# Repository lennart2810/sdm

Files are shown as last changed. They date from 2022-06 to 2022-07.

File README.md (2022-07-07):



<div align="center">
  <a href="https://www.w-hs.de/maschinenbau-master-boh/">
    Images
  </a>
</div>
<h1 align="center"> Special Topics of Mechatronics <br> Inverted Pendulum </h1>

<br/>
<div align="center">
  <a href="https://github.com/lennart2810/sdm/blob/master/CAD/assembly_screenshot.png">
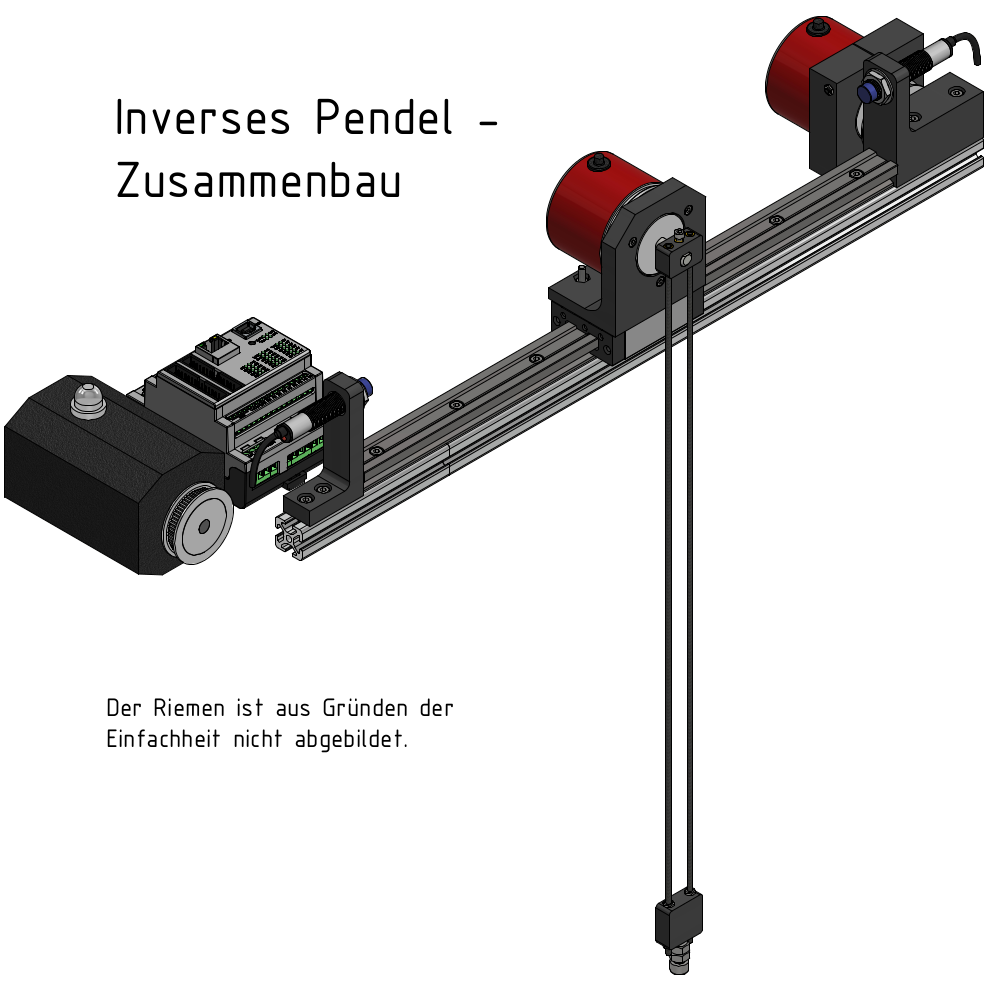
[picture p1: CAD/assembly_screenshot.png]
Images
    
  </a>
</div>
<br>

   ```sh
   git clone https://github.com/lennart2810/sdm.git
   ```

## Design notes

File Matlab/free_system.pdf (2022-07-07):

## Special Topics of Mechatronics - Inverted Pendulum

### Prepare Simscape Multibody Simulation

Import CAD files, created by Simscape Multibody Link, via Command Window:

smimport('invertedPendulum'); % .xml-file
Run invertedPendulum_DataFile.m, generated by the smimport-function, to load CAD parameter.

The data in this file sets the block parameter values in the Simscape Multibody model.

inverted_pendulum_DataFile;

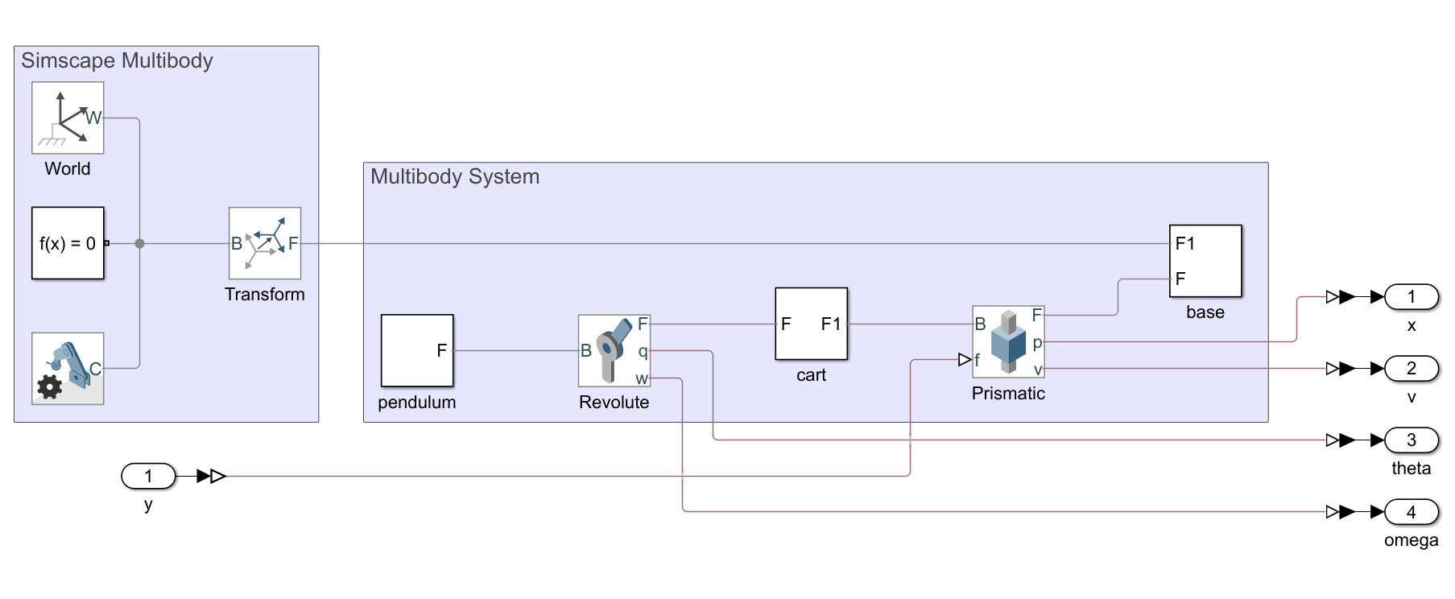
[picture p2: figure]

### Prepare Simscape Multibody Simulation

(overwrite some of the invertedPendulum_DataFile.m params)

% starting positions
x_0 = 0; | % [m] (0m --> middle of the track)
theta_0 = 4; | % [deg] (0° --> upright)

% starting velocities
v_0 = 0; | % [m/s]
omega_0 = 0; | % [deg/s]

% damping
D = 0.00001; | % [N/(m/s)] track-cart damping
d = 0.000001; | % [N*m/(deg/s)] cart-pendulum damping

### Run Simulation

filename = 'free_system.slx'; %open(filename);
sim_data = sim(filename);

### Show timeseries plots

plot(sim_data.find('x'));
hold on;
plot(sim_data.find('theta')); hold off;

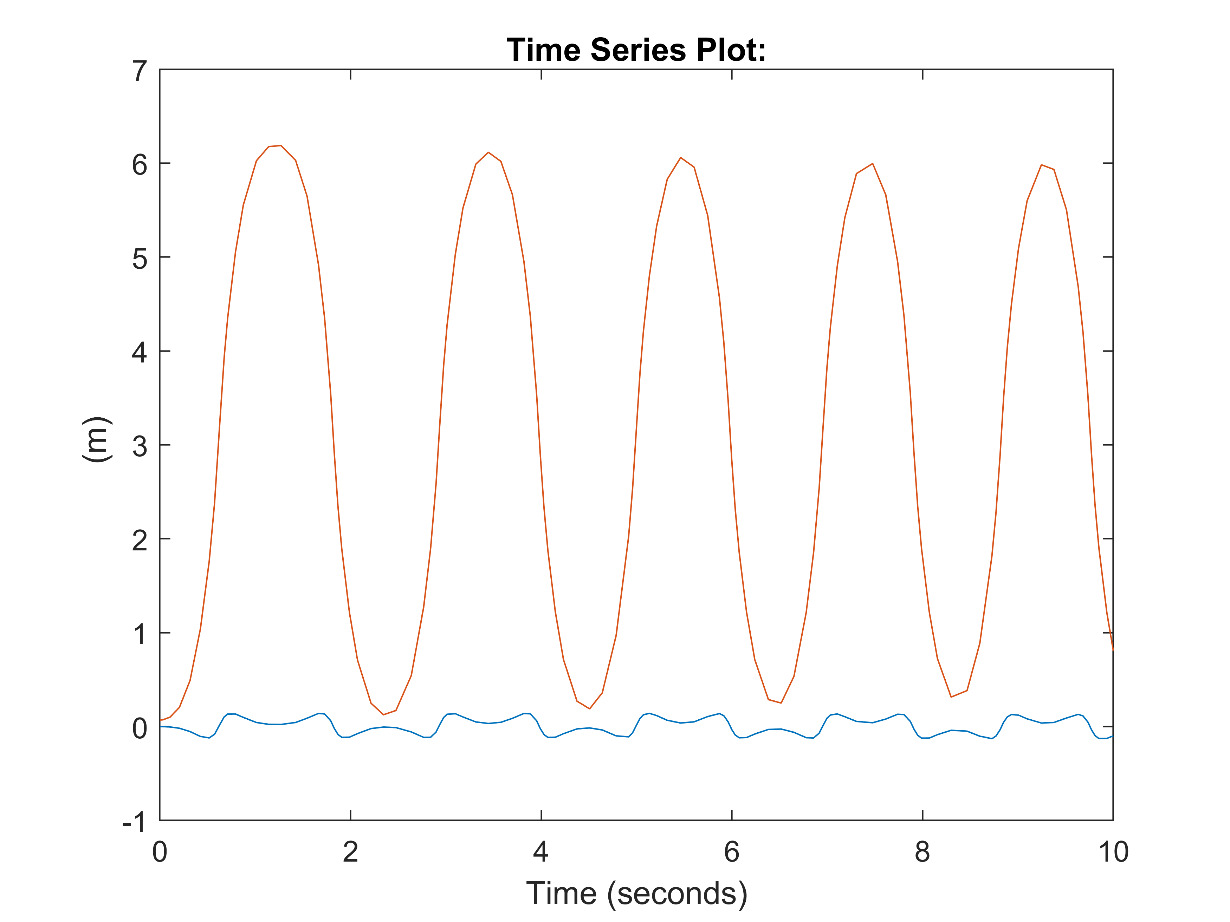
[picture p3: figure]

plot(sim_data.find('v'));
hold on;
plot(sim_data.find('omega'));

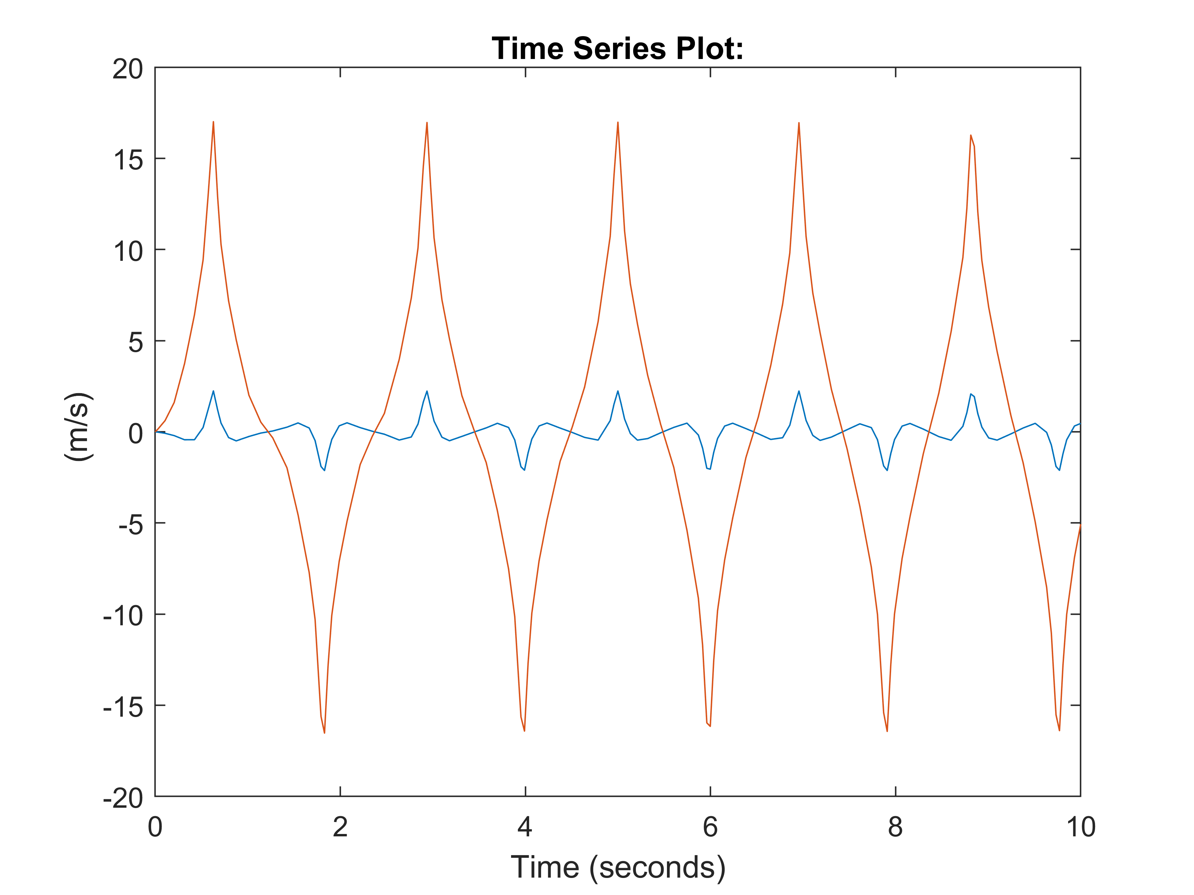
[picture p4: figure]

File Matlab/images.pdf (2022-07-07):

## Special Topics of Mechatronics - Inverted Pendulum - Images

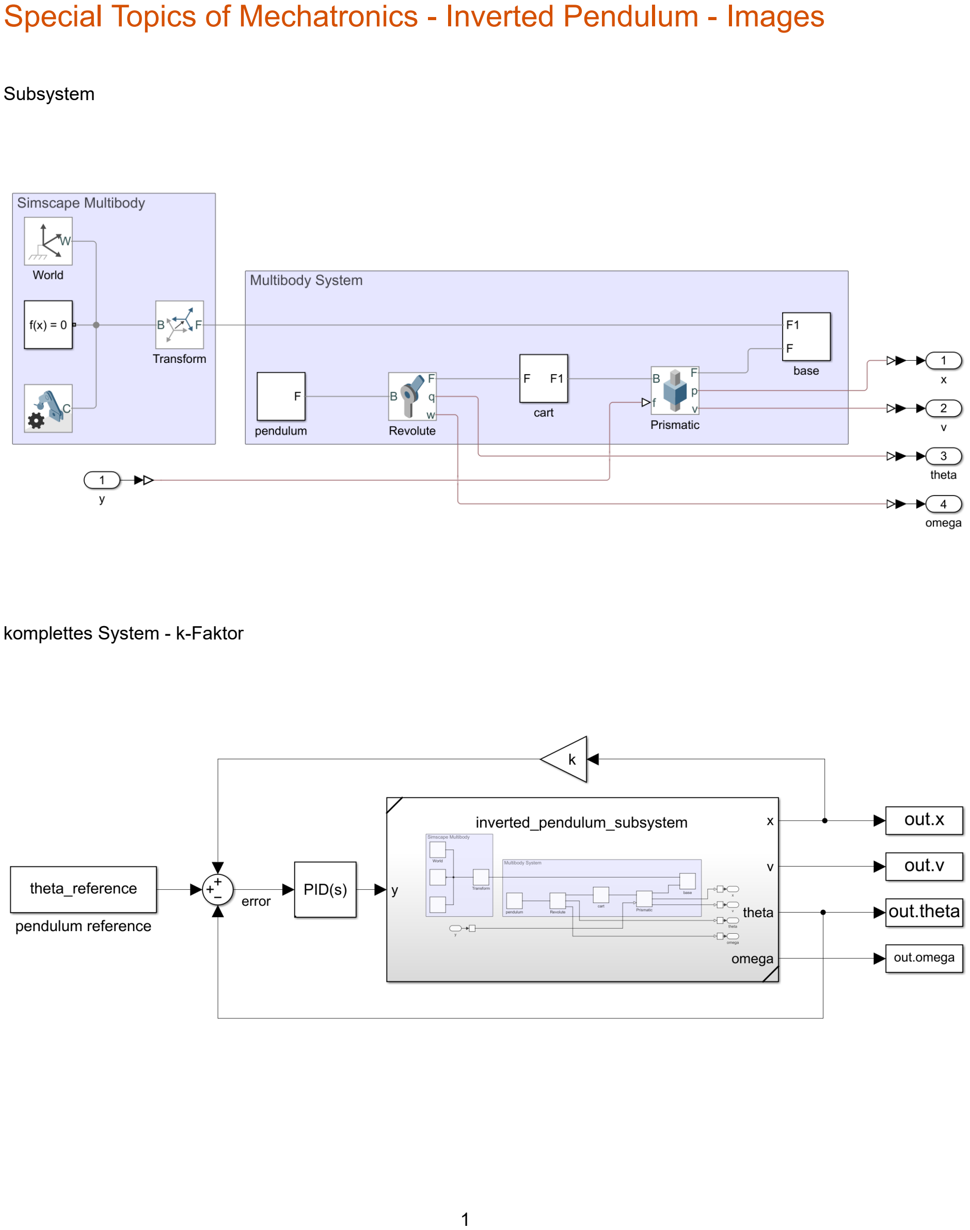
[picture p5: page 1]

Subsystem

komplettes System - k-Faktor

1

komplettes System - PID

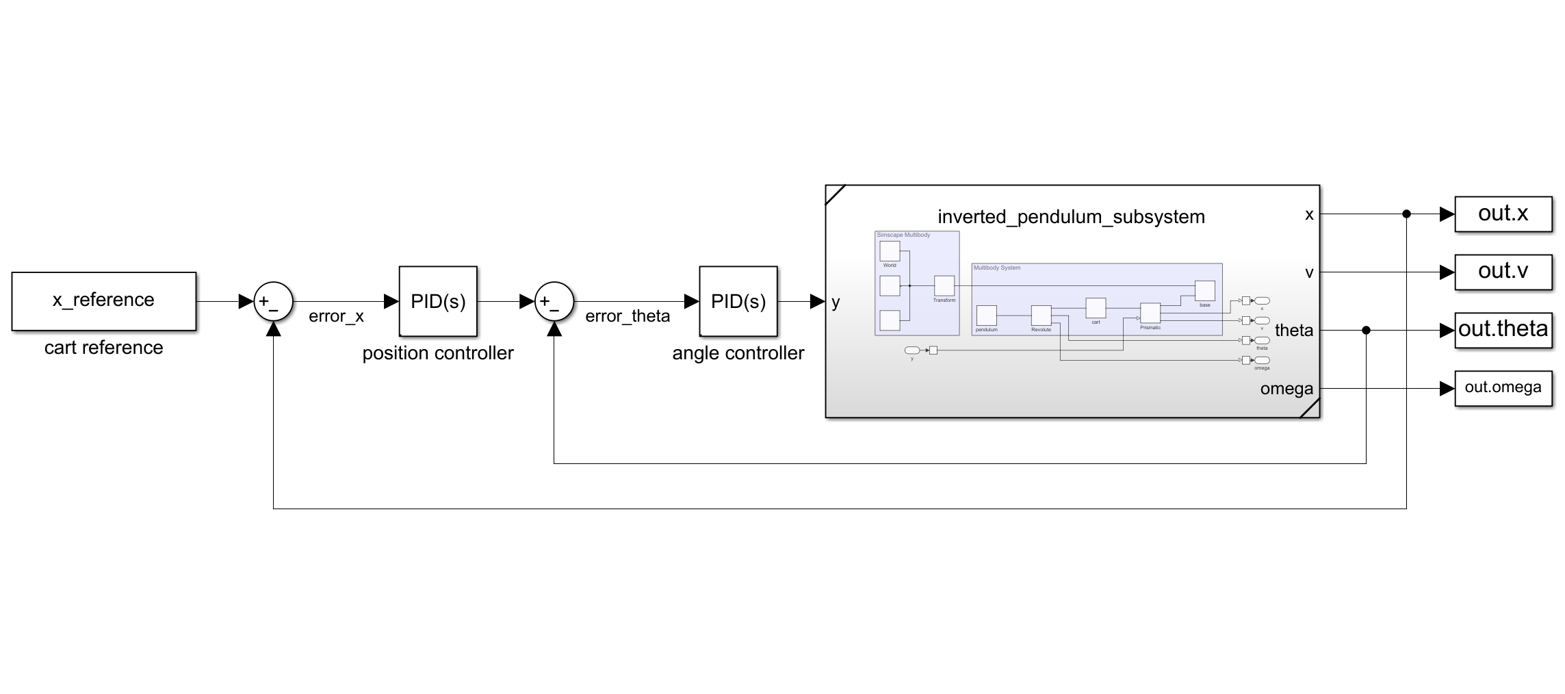
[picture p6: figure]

2

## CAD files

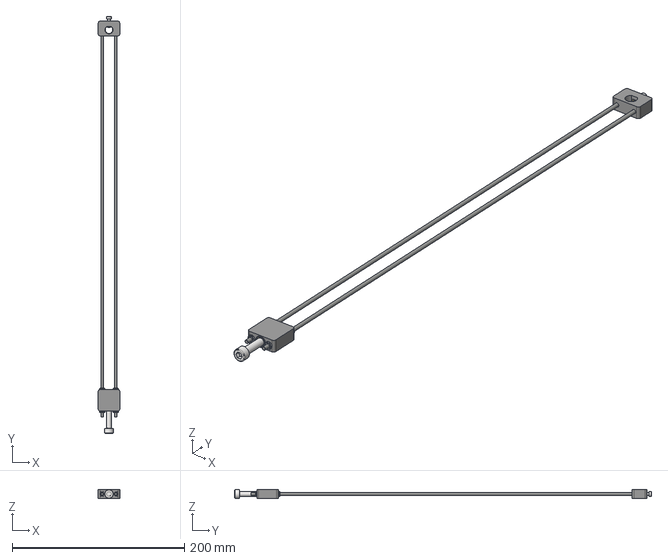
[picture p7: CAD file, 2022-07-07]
Matlab/pendulum_assembly_ipt_18ce7060.STEP
25.0 x 484.4 x 10.0 mm

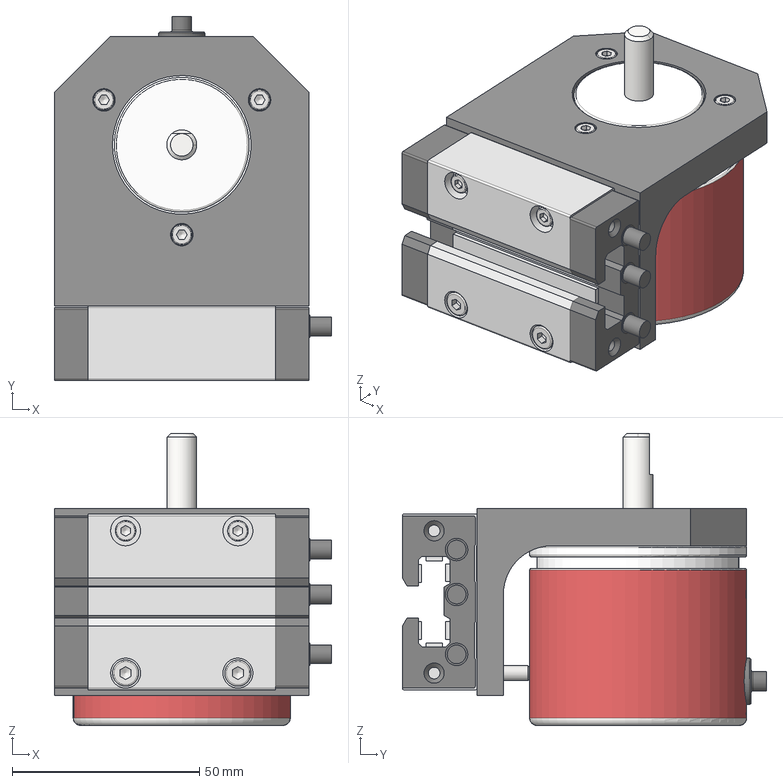
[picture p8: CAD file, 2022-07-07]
Matlab/cart_assembly_ipt_f98a6c2.STEP
74.0 x 97.3 x 78.0 mm

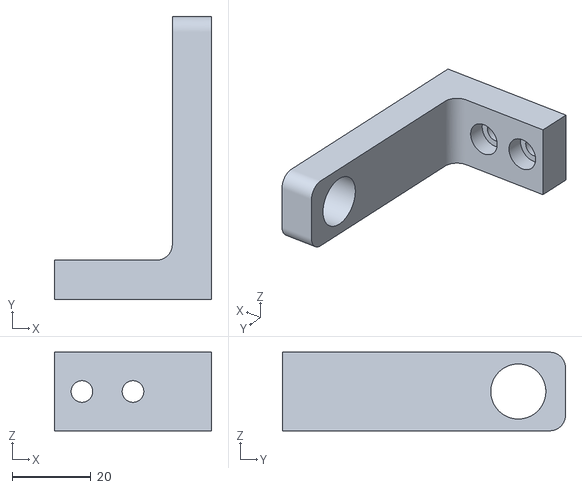
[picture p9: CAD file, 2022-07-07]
CAD/inductive_sensor_adapter.stl
40.0 x 72.0 x 20.0

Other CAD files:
CAD/M3_threaded_rod_460.ipt
CAD/M3_threaded_rod_70.ipt
CAD/M3_tread_insert.ipt
CAD/M4_groove_stone.ipt
CAD/assembly.iam
CAD/assembly_drawing.idw
CAD/base_assembly.iam
CAD/cart.ipt
CAD/cart_assembly.iam
CAD/cart_assembly.ipt
CAD/clamping_insert.ipt
CAD/dunkermotor.ipt
CAD/encoder_adapter.ipt
CAD/gt2_60.ipt
CAD/inductive_sensor.ipt
CAD/inductive_sensor_adapter.ipt
CAD/item_profile.ipt
CAD/opkon_encoder.ipt
CAD/pendulum_adapter.ipt
CAD/pendulum_assembly.iam
CAD/pendulum_assembly.ipt
CAD/pendulum_mass.ipt
CAD/pulley_positioner.ipt
CAD/rail.ipt

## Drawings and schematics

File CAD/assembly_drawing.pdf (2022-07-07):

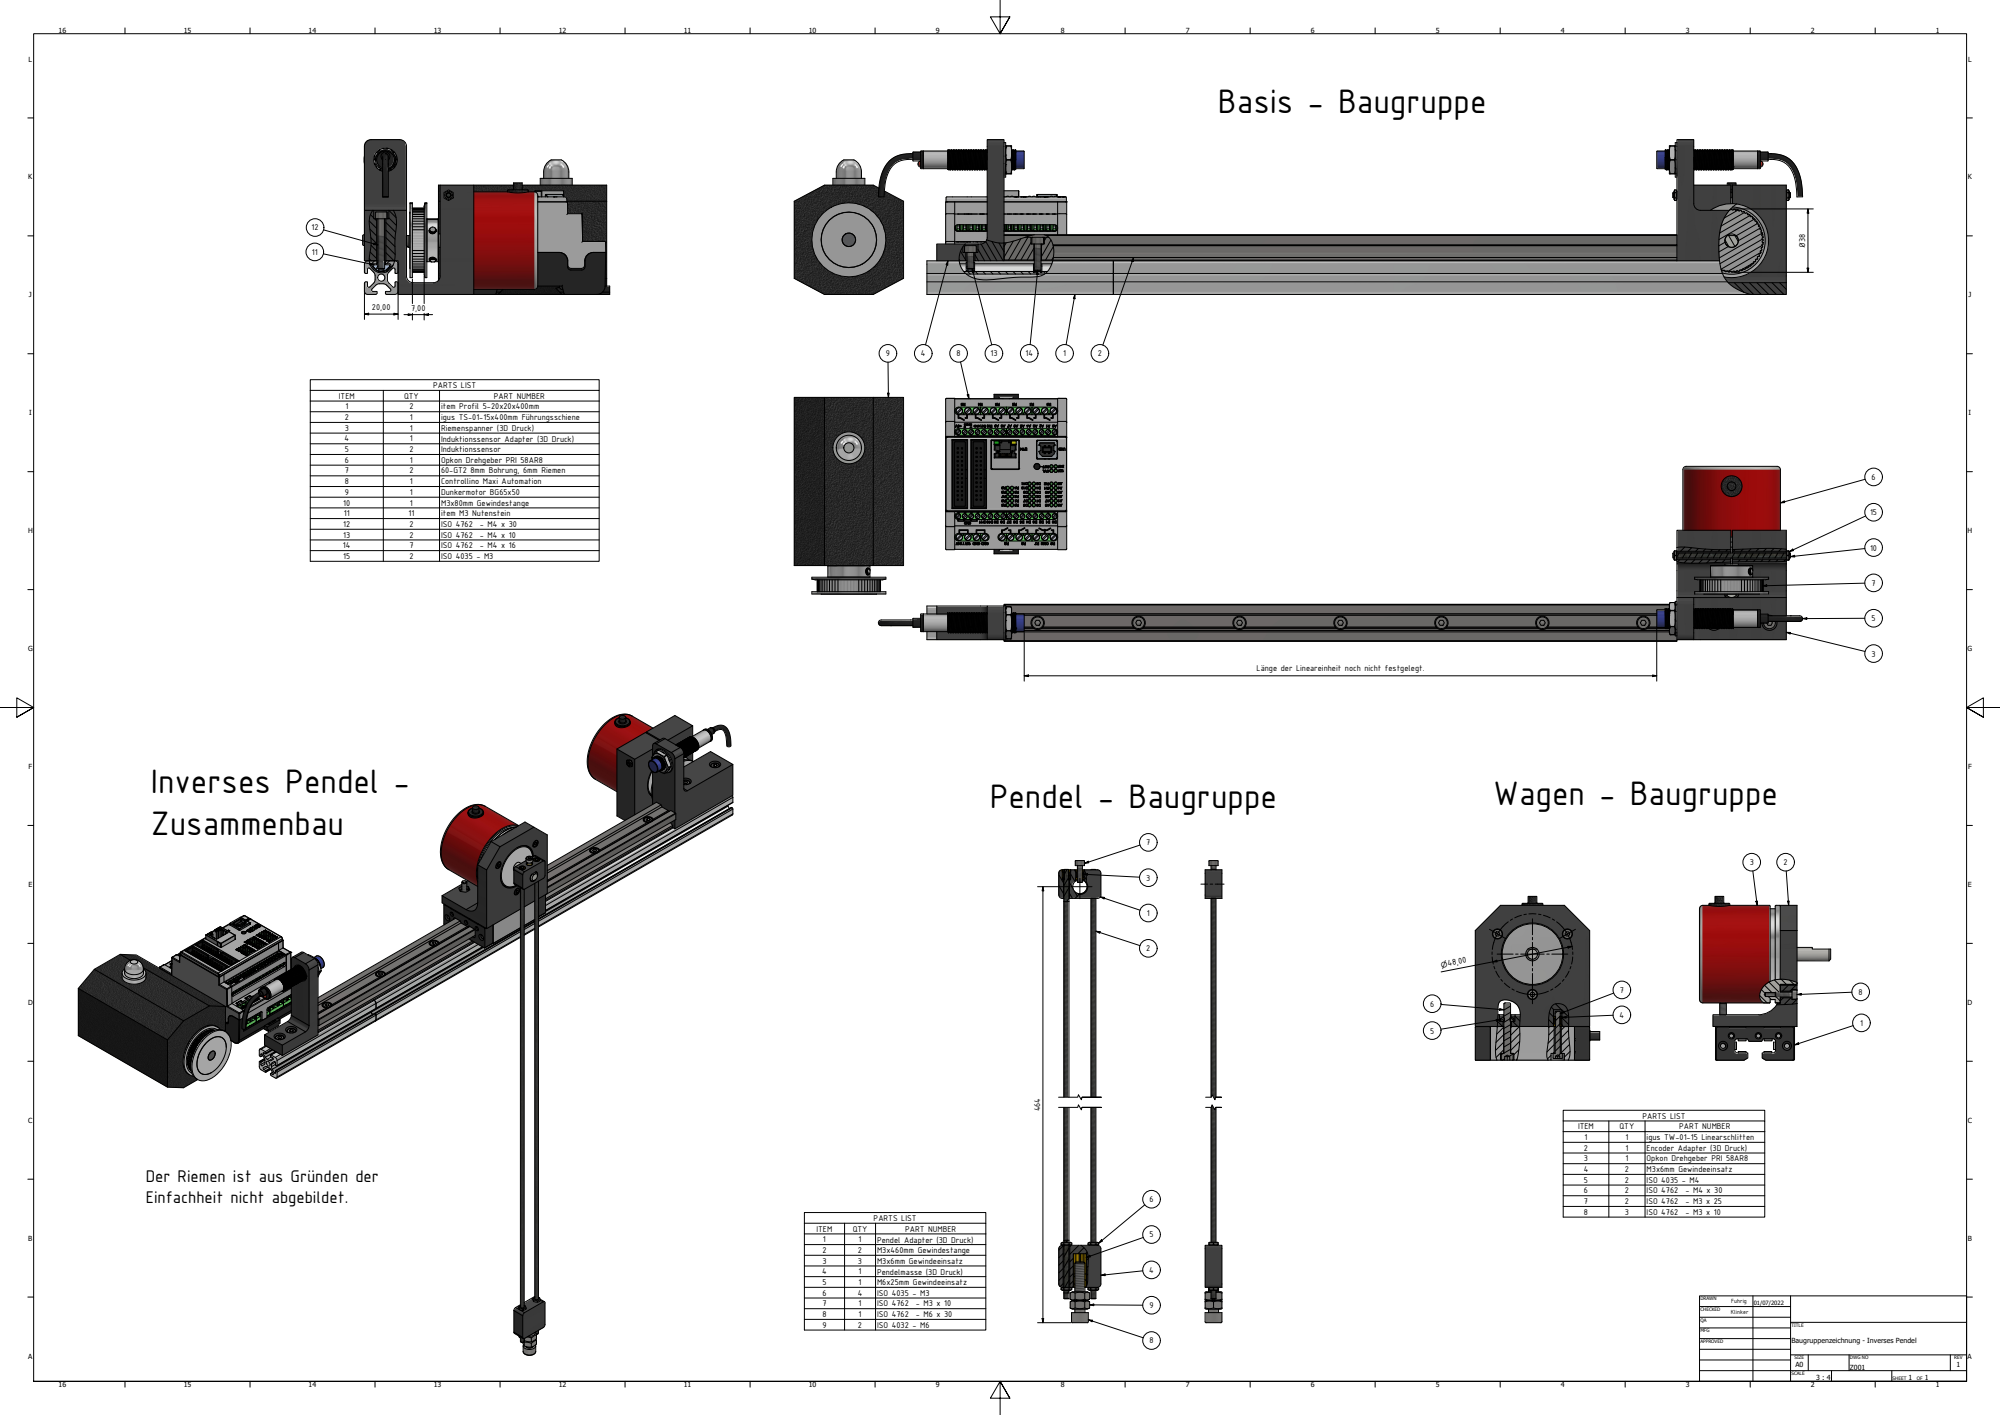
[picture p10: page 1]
PARTS LIST; ITEM; QTY; PART NUMBER; igus TW-01-15 Linearschlitten; Encoder Adapter (3D Druck); Opkon Drehgeber PRI 58AR8; M3x6mm Gewindeeinsatz; ISO 4035 - M4; ISO 4762 - M4 x 30; ISO 4762 - M3 x 25; ISO 4762 - M3 x 10; Pendel Adapter (3D Druck); M3x460mm Gewindestange; Pendelmasse (3D Druck); M6x25mm Gewindeeinsatz; ISO 4035 - M3; ISO 4762 - M6 x 30; ISO 4032 - M6; item Profil 5-20x20x400mm; igus TS-01-15x400mm F¯hrungsschiene; Riemenspanner (3D Druck); Induktionssensor Adapter (3D Druck)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

Lnge der Lineareinheit noch nicht festgelegt.

Der Riemen ist aus Gr¯nden der
Einfachheit nicht abgebildet.

Baugruppenzeichnung - Inverses Pendel

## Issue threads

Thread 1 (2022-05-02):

Documentation

KlinkerJ, 2022-05-02:
Lass uns die Dateien mal ordentlich dokumentieren @lennart2810, in drei Monaten versteht sonst keiner mehr den Unterschied zwischen [gui_test.ino](https://github.com/lennart2810/sdm/blob/master/scripts/gui_test/gui_test.ino) und [controllino_gui_lageregler.ino](https://github.com/lennart2810/sdm/blob/master/scripts/controllino_gui_lageregler/controllino_gui_lageregler.ino), dafür brauch ich aber auch noch etwas Input von Dir.

lennart2810, 2022-07-07:
Da die beiden scripte überflüssig sind, schmeißen wie sie einfach raus 😸

Closed 2022-07-07.

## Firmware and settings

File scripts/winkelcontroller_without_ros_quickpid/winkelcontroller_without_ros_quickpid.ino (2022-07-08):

#include <Controllino.h>

// Encoder
#include <Encoder.h>
#define ENC 2000   // pendel senkrecht nach oben
#define TOLROT 250 // ENC -+ 100
const byte interruptPin0 = CONTROLLINO_IN0;
const byte interruptPin1 = CONTROLLINO_IN1;
const byte digitalIn0 = CONTROLLINO_DI0;
const byte digitalIn1 = CONTROLLINO_DI1;
Encoder encoder_rot(interruptPin1, interruptPin0);

// Setpoint_rot
float Setpoint_rot = ENC / 2;
float Input_rot, Output_rot = 0;

// PIDs
#include "QuickPID.h"
float Kp_rot = 3.5, Ki_rot = 0.5, Kd_rot = 0.3;
QuickPID PID_rot(&Input_rot, &Output_rot, &Setpoint_rot);

// Motor
#define PWM_MIN 0
#define PWM_MAX 75 // 50
const int pwm_pin = CONTROLLINO_AO0;
const int motor_in1_pin = CONTROLLINO_DO1;
const int motor_in2_pin = CONTROLLINO_DO2;

// REFERENCE
const int ind_right_pin = CONTROLLINO_DI2;
const int ind_left_pin = CONTROLLINO_DI3;

// FREIGABE
int pwm_global;

void setup()
{
  Serial.begin(115200);

  // encoder
  pinMode(interruptPin0, INPUT);
  pinMode(interruptPin1, INPUT);
  pinMode(digitalIn0, INPUT);
  pinMode(digitalIn1, INPUT);

  // induktion
  pinMode(ind_right_pin, INPUT);
  pinMode(ind_left_pin, INPUT);

  // motor
  pinMode(pwm_pin, OUTPUT);
  pinMode(motor_in1_pin, OUTPUT);
  pinMode(motor_in2_pin, OUTPUT);
  // motor aktivieren ?!
  digitalWrite(motor_in1_pin, HIGH);
  digitalWrite(motor_in2_pin, LOW);

  // pid
  PID_rot.SetMode(PID_rot.Control::automatic);
  PID_rot.SetOutputLimits(-PWM_MAX, PWM_MAX);
  PID_rot.SetTunings(Kp_rot, Ki_rot, Kd_rot);
  PID_rot.SetSampleTimeUs(5000); // SampleTime auf 50ms
  delay(1000);
  encoder_rot.write(0);
}

void loop()
{
  int encoder_mod = int(abs(encoder_rot.read())) % ENC;
  bool left_pin = digitalRead(ind_left_pin);
  bool right_pin = digitalRead(ind_right_pin);

  if (left_pin == false && right_pin == false)
  {
    encoder_rot.write(0);
  }

  Input_rot = encoder_mod;
  PID_rot.Compute();
  printEncoder();
  // wenn das Pendel im regelbaren Bereich liegt..
  if (controllable() == true)
  {
    int drv = int(Output_rot);
    drive_motor(drv);
  }
  else
  {
    drive_motor(0);
  }
}

// Motor wird über Geschwindikeit angesteuert (PWM signal)
void drive_motor(int pwm)
{
  // Richtung setzen
  if (pwm > 0)
  {
    // der Motor reagiert erst ab PWM>8
    if (pwm < 10)
    {
      pwm = 10;
    }
    digitalWrite(motor_in1_pin, HIGH);
    digitalWrite(motor_in2_pin, LOW);
  }
  else
  {
    if (pwm > -10)
    {
      pwm = -10;
    }
    digitalWrite(motor_in1_pin, LOW);
    digitalWrite(motor_in2_pin, HIGH);
  }
  pwm_global = pwm;
  int abs_int = abs(pwm);
  analogWrite(pwm_pin, int(abs_int));
}

void printEncoder()
{
  if (!Serial)
  {
    return;
  }
  Serial.print(Input_rot);
  Serial.print("\t");
  Serial.println(pwm_global);
}

bool controllable()
{
  // true wenn Pendel im regelbaren Bereich liegt (ENC+-TOLROT)
  int grenze1 = ENC / 2 - TOLROT;
  int grenze2 = ENC / 2 + TOLROT;
  if (Input_rot >= grenze1 && Input_rot <= grenze2)
  {
    return true;
  }
  else
  {
    return false;
  }
}

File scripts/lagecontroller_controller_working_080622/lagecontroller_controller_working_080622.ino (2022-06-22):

#include <ros.h>
#include <std_msgs/Empty.h>
#include <std_msgs/Int32.h>
#include <std_msgs/Float32MultiArray.h>
#include <std_msgs/Int32MultiArray.h>

#include <Controllino.h>

ros::NodeHandle  nh;

//Left- & Right-Position
#define LEFTPOS 10000
#define RIGHTPOS 2500
#define MAXSPEED 45

// SETPOINT
volatile double Setpoint = 5000;
double Input, Output = 0;
bool referenced = false;
//volatile int setpoint = 0;
//const int setpoint_led = 7;

volatile int speed = 0;
void setpointCb(const std_msgs::Int32& setpoint_msg) {
  Setpoint = setpoint_msg.data;
  //speed = setpoint_msg.data;
  //drive_motor(setpoint_msg.data/100); // setpooint als motorgeschwindigkeit verwenden!!!
}
ros::Subscriber<std_msgs::Int32> setpoint_sub("setpoint", setpointCb);

// PIDs
#include <PID_v1.h>
double Kp = 0.01, Ki = 0, Kd = 0;
PID myPID(&Input, &Output, &Setpoint, Kp, Ki, Kd, DIRECT);

void pidsCb(const std_msgs::Int32MultiArray &pids_msg) {
  Kp = pids_msg.data[0] / 100.0;
  Ki = pids_msg.data[1] / 100.0;
  Kd = pids_msg.data[2] / 100.0;
  myPID.SetTunings(Kp, Ki, Kd);
}
ros::Subscriber<std_msgs::Int32MultiArray> pids_sub("pids", pidsCb);

// Motor
#define PWM_MIN 0
#define PWM_MAX 30
//bool dir = true; // true --> cw
const int pwm_pin = CONTROLLINO_AO0;
const int motor_in1_pin = CONTROLLINO_DO1;
const int motor_in2_pin = CONTROLLINO_DO2;

// Encoder
#include <Encoder.h>
#define ENC 500            // pulses per revolution (with Encoder.h)
const byte interruptPin0 = CONTROLLINO_IN0;
const byte interruptPin1 = CONTROLLINO_IN1;
const byte digitalIn0 = CONTROLLINO_DI0;
const byte digitalIn1 = CONTROLLINO_DI1;
Encoder encoder0(interruptPin0, digitalIn0);
Encoder encoder1(interruptPin1, digitalIn1);
std_msgs::Int32 enc_msg;
ros::Publisher enc_pub("enc", &enc_msg);

// REFERENCE
const int ind_pin = CONTROLLINO_DI2;

void referenceCb( const std_msgs::Empty& reference_msg) {
  reference();
}
ros::Subscriber<std_msgs::Empty> ref_sub("reference", &referenceCb );

void setup()
{
  pinMode(interruptPin0, INPUT);
  pinMode(interruptPin1, INPUT);
  pinMode(digitalIn0, INPUT);
  pinMode(digitalIn1, INPUT);

  pinMode(ind_pin, INPUT);

  pinMode(pwm_pin, OUTPUT);
  pinMode(motor_in1_pin, OUTPUT);
  pinMode(motor_in2_pin, OUTPUT);

  myPID.SetOutputLimits(-PWM_MAX, PWM_MAX);
  myPID.SetMode(AUTOMATIC);

  //delay(500);

  nh.initNode();
  nh.advertise(enc_pub);
  nh.subscribe(setpoint_sub);
  nh.subscribe(pids_sub);
  nh.subscribe(ref_sub);

  // motor aktivieren ?!
  digitalWrite(motor_in1_pin, HIGH);
  digitalWrite(motor_in2_pin, LOW);

  //delay(2000);

  //Serial.begin(115200);

  reference();
}

void loop()
{
  //erst ausführen, wenn referenziert wurde
  if (referenced == true) {
    Input = encoder0.read();
    //Input = analogRead(adc_pin);
    myPID.Compute();
    //Serial.println(-Output);
    //drive_motor(-10);
    drive_motor(int(-Output));
    enc_msg.data = Input;
    enc_pub.publish( &enc_msg );
  }
  nh.spinOnce();
}

bool allowMovement(int pwm)
{
  if (digitalRead(ind_pin) == false && pwm > 0) {
    return false;
  }

  //Positionsüberprüfung erst ausführen, wenn referenziert wurde
  if (referenced == true) {
    int currentPosition = Input;
    //wenn linker Anschlag und Fahrtrichtung nach links
    if (currentPosition > LEFTPOS && pwm < 0) {
      return false;
    }
    //wenn rechter Anschlag und Fahrtrichtung nach rechts
    if (currentPosition < RIGHTPOS && pwm > 0) {
      return false;
    }
  }
  return true;
}

void drive_motor(int pwm)
{
  if (allowMovement(pwm) == true) {

    if (pwm >= 0) {
      digitalWrite(motor_in1_pin, HIGH);
      digitalWrite(motor_in2_pin, LOW);
    }

    else {
      digitalWrite(motor_in1_pin, LOW);
      digitalWrite(motor_in2_pin, HIGH);
    }

    analogWrite(pwm_pin, int(abs(pwm)));
  } else {
    speed = 0;
    digitalWrite(motor_in1_pin, LOW);
    digitalWrite(motor_in2_pin, LOW);
    analogWrite(pwm_pin, int(0));
  }
}

void reference()
{
  // nach links fahren bis induction aktiviert wird
  while (digitalRead(ind_pin) == true)
  {
    drive_motor(10);
  }

  drive_motor(0);
  delay(1000);
  encoder0.write(0);
  referenced = true;
  delay(2500);
}

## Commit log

2022-04-16 motor driver
2022-04-24 encoder arduino uno
2022-07-07 add matlab and cad files, clean up scripts folder
    [M3_threaded_rod_460.ipt, M3_threaded_rod_70.ipt, M3_tread_insert.ipt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]
